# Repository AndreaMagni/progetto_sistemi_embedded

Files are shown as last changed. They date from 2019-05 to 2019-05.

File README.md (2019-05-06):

# Progetto Sistemi Embedded
Corso di Sistemi Embedded - Università degli Studi di Milano - Anno accademico 2017/2018

### Autori:
Magni Andrea - Mercanti Davide

### Descrizione progetto:
Il progetto che abbiamo deciso di realizzare prevede la costruzione di una "macchina intelligente".

La macchina andrà a svolgere diverse funzioni, principalmente di comunicazione o di valutazione e risoluzione di problematiche, tra le quali:

- riuscire a muoversi all'interno di una strada composta da due corsie, rimanendo all'interno di una corsia
- riuscire ad effettuare una manovra di cambio corsia
- valutare la presenza di un semaforo
  - nel caso in cui venga rilevato un semaforo valuti la sua condizione e regoli la velocità di conseguenza
- valutare la presenza di possibili ostacoli durante il percorso
  - nel caso in cui venga rilevato un ostacolo valuti il tipo di ostacolo (mobile o fisso) e decida se continuare il 
  percorso o effettuare una manovra di cambio corsia
- comunicare con un telefono per permettere lo scambio di informazioni tra la macchina e l'utente in diretta

### Componenti necessari:
- x1 | Arduino MEGA | https://www.amazon.it/gp/product/B06XRJNB27/ (necessario per la macchina, la quale richiede molti GPIO)
- x1 | Board generica per gestire il semaforo, il quale non necessità di molti GPIO
- x1 | 4 Motori - 4 Ruote - Scocca | https://www.amazon.it/gp/product/B073169GBF/ (si possono utilizzare solo due ruote/motori con una terza ruota girevole https://www.amazon.it/dp/B072ZWRM2B/)
- x2 | Modulo gestione motori - L298N | https://www.amazon.it/gp/product/B013QTC18K/ (si può utilizzare un solo modulo gestendo i motori a coppie)
- x2 | Modulo radio - NRF24L01 | https://www.amazon.it/gp/product/B016BAPC0K/ (si possono utilizzare eventualmente dei moduli Wi-Fi o Bluetooth)
- x1 | Modulo bluetooth - HC-05 | https://www.amazon.it/dp/B01G9KSAF6/
- x4 | Sensore ad infrarossi - TE174 o FC-35 | https://www.amazon.it/gp/product/B00XXEJD58/ 
- x3 | Sensore ad ultrasuoni - HC-SR04 | https://www.amazon.it/gp/product/B00R2U8HK6/
- x1 | Resistenza da 8.2 ohm (in alternativa 10)
- x3 | Resistenza da 220 ohm
- x1 | Resistenza da 1 Kohm
- x1 | Resistenza da 2.2 Kohm
- x1 | Resistenza da 10 Kohm
- Componenti vari come breadboard e cavetteria

### Sviluppo del progetto:
- Realizzazione di una macchina, la quale deve:
  - potersi muovere attraverso il controllo, in modo indipendente, della velocità e verso dei _**quattro motori DC**_. Questa funzionalità è permessa dalla presenza di due _**moduli gestione motori**_. Nello specifico per questo progetto viene utilizzato il _**modulo gestione motori L298N**_, il quale permette la gestione del verso e della potenza di due motori in modo indipendente.
  - valutare la corsia da seguire all'interno del tratto stradale. Per questa funzionalità abbiamo deciso di creare un inseguitore di linea, tramite dei _**sensori ad infrarossi**. 
  - valutare la presenza di ostacoli nel suo percorso tramite dei _**sensori ad ultrasuoni**_
  - valutare lo stato dei semafori tramite un _**modulo radio**_
- Realizzazione di una strada:
  - le opzioni per questo punto erano due, da un lato la semplice creazione di delle strisce nere da posizionare sul pavimento per permettere ai sensori ad infrarossi di valutare la strada da seguire oppure realizzare una strada vera e propria. Abbiamo deciso di realizzare una strada tramite del polistirolo cartonato, disegnando le linee tramite degli indelibili neri. La strada è composta da un totale di quattro linee, ogni corsia da due. La linea meno spessa serve alla macchina per stabilire da quale lato della strada si trova in modo da effettuare la giusta manovra nel caso in cui debba effettuare un cambio corsia. 
- Realizzazione di un semaforo, il quale deve:
  - effettuare un cambiamento di stato tra "verde giallo rosso".
  - comunicare con la macchina lo stato del semaforo
  
### Schema collegamenti macchina:
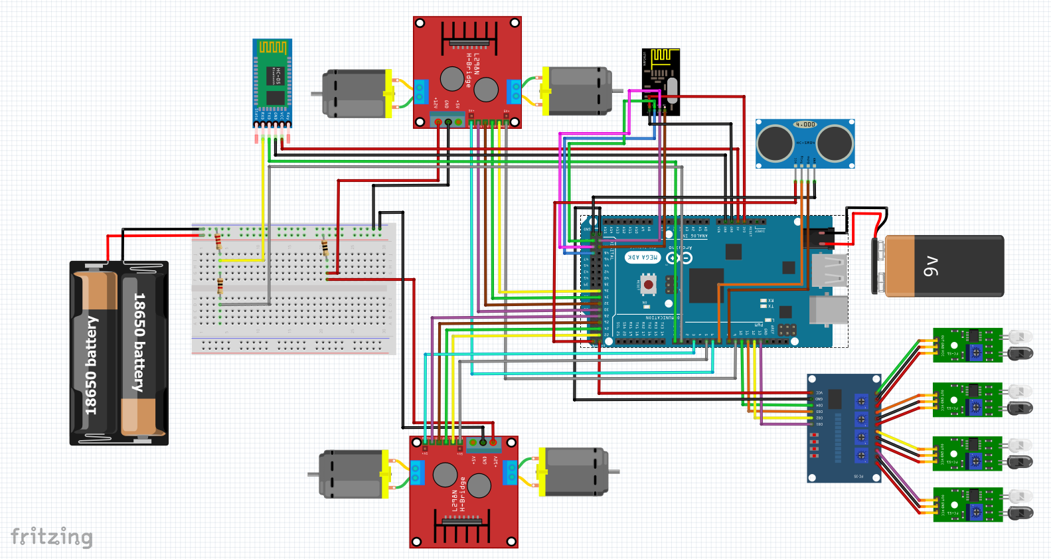
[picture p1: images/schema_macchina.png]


### Schema collegamenti semaforo:
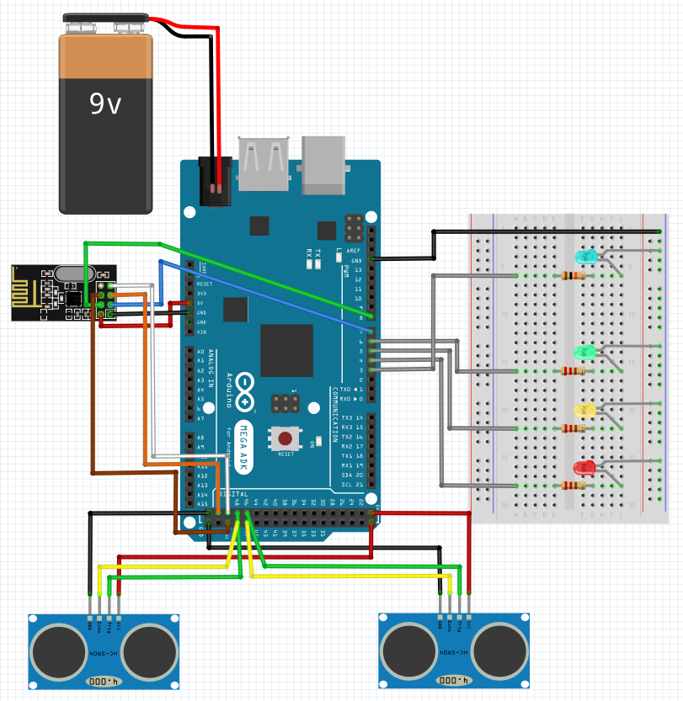
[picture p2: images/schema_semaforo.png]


### Foto:
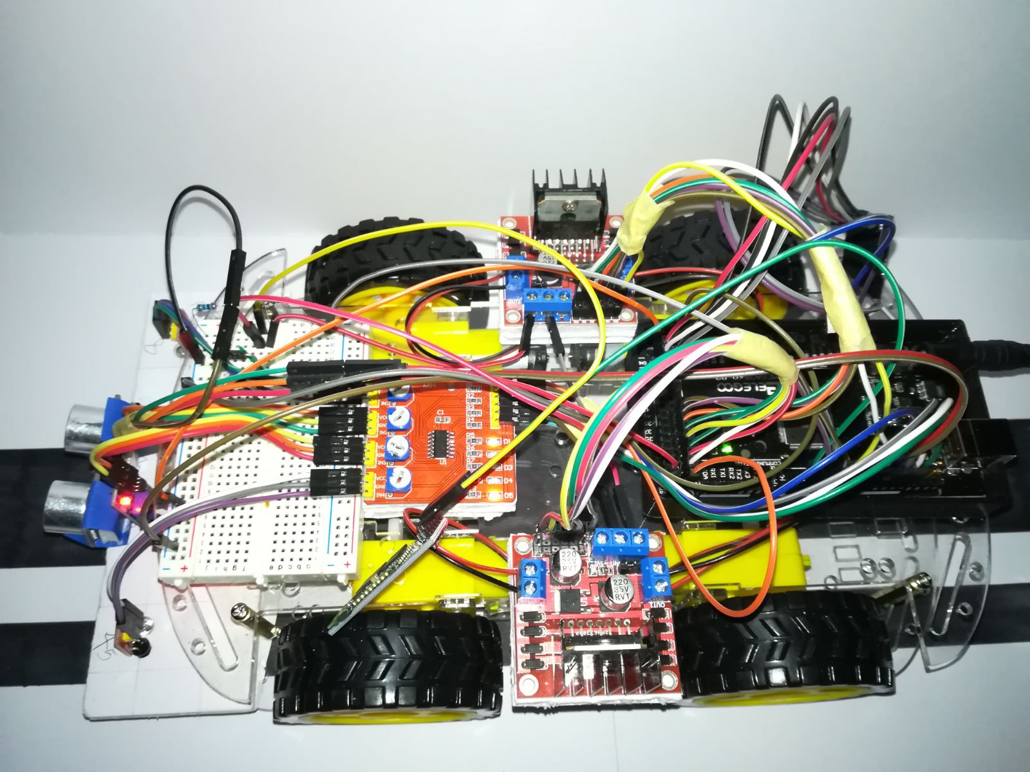
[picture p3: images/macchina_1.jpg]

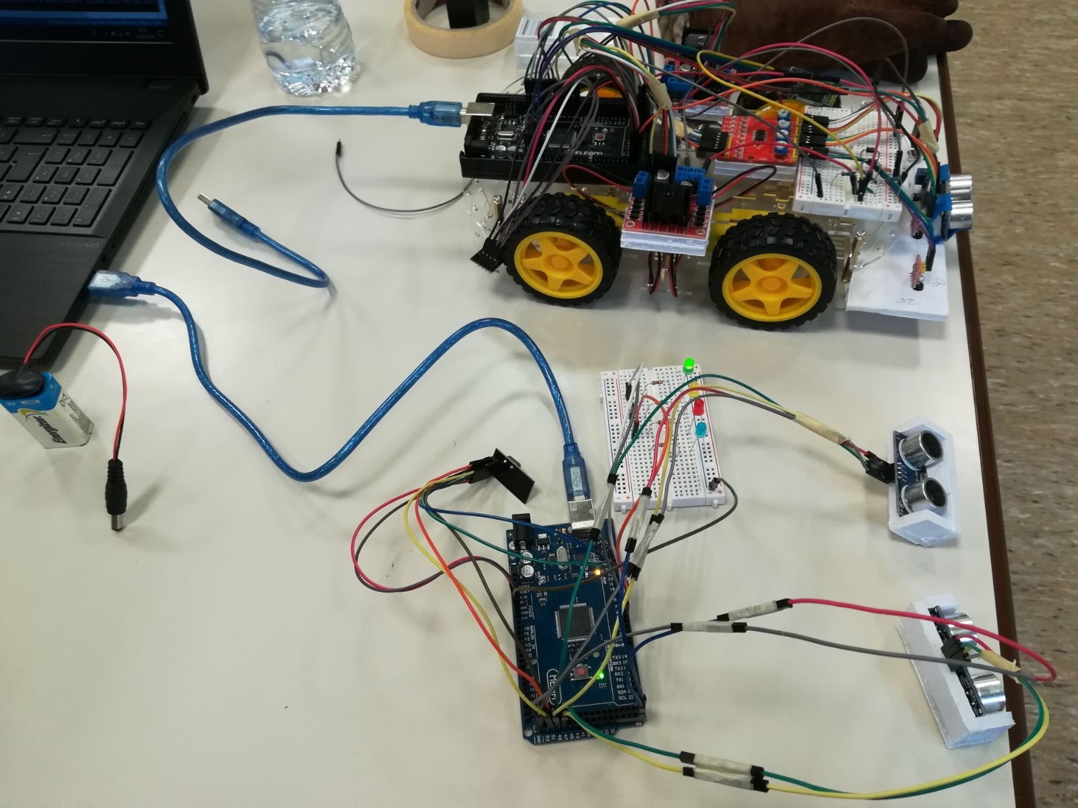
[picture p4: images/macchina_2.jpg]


### Video: 

Test sistema di gestione delle curve tramite servo:  
https://www.dropbox.com/s/mpuvc6oca1bey50/1_vecchio_sistema_curva.mp4?dl=0

Test sistema di gestione delle curve tramite velocità differenti sulle ruote:  
https://www.dropbox.com/s/kdcqv2tspdruida/2_nuovo_sistema_curva.mp4?dl=0

Test inseguitore di linea tramite infrarossi:  
https://www.dropbox.com/s/6vckf1oelf2ck3c/3_infrarossi_curva.mp4?dl=0

Test gestione velocità tramite ultrasuoni:  
https://www.dropbox.com/s/164yps8jlzu4az5/4_sonar_stop.mp4?dl=0

Prototipo finale con tracciato, gestione ostacolo fisso:  
https://www.dropbox.com/s/opallh4xtinxfd5/5_ostacolo_singolo.mp4?dl=0

Prototipo finale con tracciato, gestione doppio ostacolo fisso:  
https://www.dropbox.com/s/qxkiae7qwjshndc/6_doppio_ostacolo.mp4?dl=0

### Librerie aggiuntive:
- RF24.h (modulo radio): https://github.com/nRF24/RF24
- NewPing.h (sensore ultrasuoni): https://playground.arduino.cc/Code/NewPing
- Motor.h (gestione motori): https://github.com/AndreaMagni/SistemiEmbedded/tree/master/Car

### Possibili upgrade:
- Realizzazione di un sistema di semafori, ad esempio un incrocio, il quale valuti la presenza di cose di macchine nelle varie strade e decida come impostare i semafori in modo intelligente.
- Realizzazione di un sistema GPS per tenere traccia degli spostamenti della macchina, probabilmente sulla piccola scala dei movimenti della macchina potrebbe essere difficile o inutile da sviluppare ma potrebbe portare ad idee alternative collegate.
- Realizzazione di un collegamento tra la macchina e Processing scrivendo del codice per ricreare il tracciato percorso dalla macchina durante ogni sessione di utilizzo.
- Realizzazione di un sistema di sterzo per permettere alla macchina di curvare.
- Realizzazione di un sonar mobile, creato unendo un sensore ad ultrasuoni ad un servomotore. In questo modo sarebbe possibile analizzare le distanze degli oggetti non solo se frontali rispetto al modulo ad ultrasuoni ma anche attorno ad esso.
- Realizzazione di un passaggio a livello tramite un servomotore

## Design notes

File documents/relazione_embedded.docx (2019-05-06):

DESCRIZIONE FUNZIONALITA’

Il progetto che abbiamo deciso di realizzare prevede la costruzione di una "macchina intelligente".

La macchina andrà a svolgere diverse funzioni, principalmente di comunicazione o di valutazione e risoluzione di problematiche, tra le quali:

- riuscire a muoversi all'interno di una strada composta da due corsie, rimanendo all'interno di una corsia
- riuscire ad effettuare una manovra di cambio corsia
- valutare la presenza di un semaforo
  - nel caso in cui venga rilevato un semaforo valuti la sua condizione e regoli la velocità di conseguenza
- valutare la presenza di possibili ostacoli durante il percorso
  - nel caso in cui venga rilevato un ostacolo valuti il tipo di ostacolo (mobile o fisso) e decida se continuare il percorso o effettuare una manovra di cambio corsia
- comunicare con un telefono per permettere lo scambio di informazioni tra la macchina e l'utente in diretta

ELENCO COMPONENTI

Quantità | Componente | Link Amazon
1 | Board Arduino Mega | https://www.amazon.it/dp/B06XRJNB27/
1 | Board generica (non sono necessari molti GPIO) | https://www.amazon.it/dp/B01MRJR8UF/
1 | Kit telaio ruote motori | https://www.amazon.it/dp/B073169GBF/
| | https://www.amazon.it/dp/B072ZWRM2B/
2 | Modulo gestione motori - L298N | https://www.amazon.it/dp/B013QTC18K/
2 | Modulo radio - nRF24L01 | https://www.amazon.it/dp/B016BAPC0K/
1 | Modulo bluetooth - HC-05 | https://www.amazon.it/dp/B01G9KSAF6/
4 | Sensore ad infrarossi - TE174 o FC-35 | https://www.amazon.it/dp/B00XXEJD58/
3 | Sensore ad ultrasuoni - HC-SR04 | https://www.amazon.it/dp/B00R2U8HK6/
1 | Resistenza x | https://www.amazon.it/ dp/B00J02WSFE/
1 | Resistenza x
1 | Resistenza x AL POSTO DEI DIODI
2 | Breadboard | https://www.amazon.it/ dp/B06XRDRT2R/
1 | Cavetteria | https://www.amazon.it/ dp/B01N40EK6M/ (https://www.amazon.it/%20dp/B01N40EK6M/)

DESCRIZIONE COMPONENTI UTILIZZATI

Per la creazione di questo progetto sono stati utilizzati diversi componenti, aggiungendo sempre più funzionalità potendo così testare il funzionamento di diversi sensori e moduli con relative interazioni all’interno di un singolo progetto. Andremo ora ad analizzare i vari componenti:

Telaio / Motori / Ruote

Per realizzare questo progetto è fondamentale una scocca che permetta alla macchina di sostenere i vari componenti e successivamente, una volta realizzato il codice e inseriti i vari sensori e moduli, muoversi all’interno del tracciato.

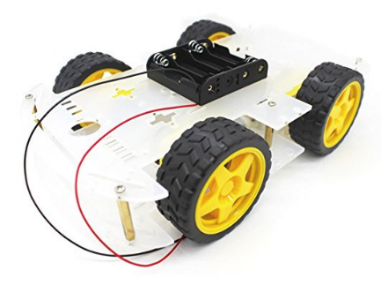
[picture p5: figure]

Sicuramente è un componente il cui acquisto non è necessario (sarebbe stato possibile crearlo attraverso del cartone) avendo però la necessità di comprare delle ruote e relativi motori a corrente continua la differenza di costo tra il comprare un kit telaio/motori/ruote oppure delle ruote e motori singolarmente era irrosoria se non addirittura più conveniente. Abbiamo quindi optato per questo telaio realizzato in plexiglass. I motori messi a disposizione nel kit sono dei comunissimi motori a corrente continua ai quali è possibile fornire una tensione massima di 6 Volt. Le ruote sono un mix di plastica e gomma.

Per quanto questo kit abbia comportato grandi comodità, bisogna anche dire che i motori non sono particolarmente precisi. Questo comporta la presenza di piccole imprecisioni durante la guida automatica della macchina che possono essere notate durante il suo percorso. Non dovendo però andare a realizzare un progetto che punta sulla precisione, la comodità portata dal kit unita al costo irrosorio ne fanno un acquisto decisamente sensato per il progetto.

Modulo L298N

Questo modulo è sicuramente un acquisto necessario quando si vuole realizzare un progetto di questo genere.

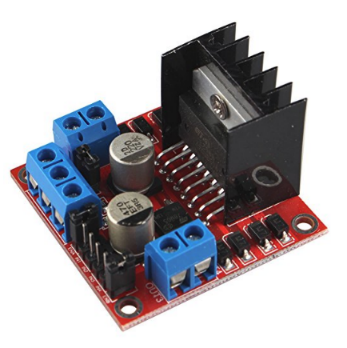
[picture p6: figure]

Il modulo L298N è utilizzato per comandare fino ad un massimo di due motori a corrente continua, può funzionare con tensioni che variano dai 5 ai 35 Volt e fornire sino a 2 Ampere di corrente per ogni uscita. Particolarmente utile la presenza di un’uscita stabile a 5 Volt, la quale può essere utilizzata per alimentare Arduino, dei componenti oppure per far passare 5 Volt sulla breadboard.

Per il progetto sono stati utilizzati due di questi componenti, potendo così gestire singolarmente ogni motore. Questa soluzione non è necessaria in quanto si potrebbe utilizzare un solo modulo collegando in parallelo a coppie i motori.

Modulo nRF24L01

Questo modulo viene utilizzato per creare un canale radio attraverso il quale comunicare. Esso non è necessario nel momento in cui si vuole costruire un semplice line follower, invece può risultare molto utile nel momento in cui si voglia comunicare con altri componenti (ad esempio un radiocomando per controllare la macchina).

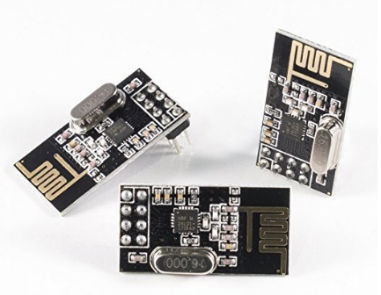
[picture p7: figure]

All’interno del progetto è stato inserito per permettere la comunicazione con un secondo Arduino, all’interno del quale è caricato un programma che simula un semaforo.

Il semaforo e la macchina potranno quindi comunicare tra loro, nello specifico sarà il semaforo che potrà inviare alla macchina il suo stato, la macchina andrà ad analizzare lo stato corrente e valuterà in base allo stato come comportarsi.

Modulo HC-05

Questo modulo non è sicuramente un acquisto necessario per il progetto, in quanto un eventuale connessione tra Arduino e un secondo Arduino è già permessa dal modulo radio.

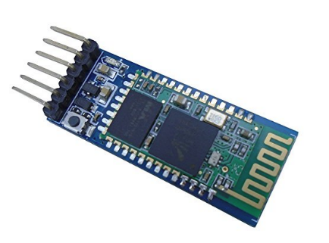
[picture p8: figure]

La scelta di aggiungere un modulo la cui funzione è quella di creare una connessione Bluetooth è stata fatta per due motivi, il principale è quello di poter comunicare con un telefono tramite una delle tante applicazioni presenti sugli store e poter così effettuare un debug in live, molto utile per determinare problemi nel comportamento della macchina in fase di progettazione. In precedenza al posto del Bluetooth era presente un display LCD sul quale venivano mostrate le informazioni. Il secondo motivo è la possibilità di avere una connessione senza fili con un PC con cui scambiare dati nel caso in cui si vogliano sviluppare in futuro delle applicazioni con Processing per visualizzare il movimento della macchina.

Sensore HC-SR04

Questo sensore permette di valutare la distanza tra esso ed un oggetto tramite l’utilizzo di ultrasuoni.

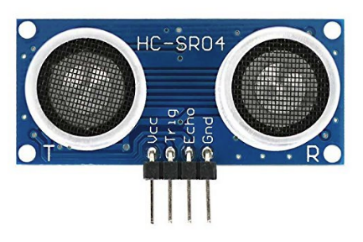
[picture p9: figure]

Trova un doppio utilizzo all’interno del progetto poiché risulta utile sia per la macchina che per il semaforo. Per la macchina la sua funzione è quella di permettere alla macchina di valutare la presenza di eventuali ostacoli di fronte al suo percorso, invece per quanto riguarda il semaforo il suo utilizzo è quello di creare una zona di apertura e una di chiusura di invio del segnale radio, impedendo cosi eventuali problemi dati da un segnale continuo.

Sensore FC-35 / FC-51

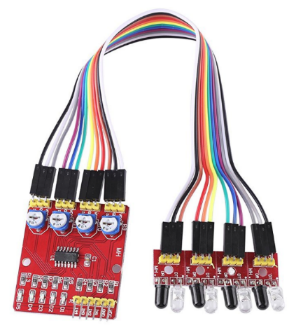
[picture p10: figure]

Questo modulo viene utilizzato per creare Questo modulo viene utilizzato per creare

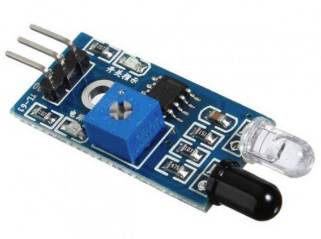
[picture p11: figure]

Questo modulo viene utilizzato per creare

Questo modulo viene utilizzato per creare

Questo modulo viene utilizzato per creare

Componentistica varia

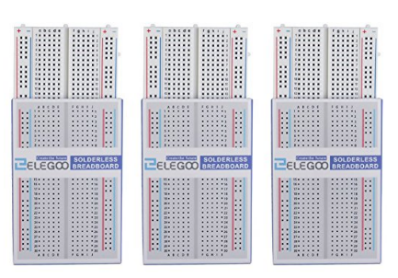
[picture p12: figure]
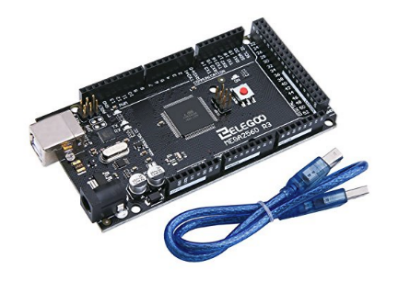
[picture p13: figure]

Per concludere, gli altri componenti utilizzati per il progetti sono una piattaforma Arduino Mega e relativa breadboard per comandare i vari moduli e sensori della macchina, un secondo Arduino Mega con breadboard per creare il semaforo.

Inoltre è stata usata molta cavetteria, dei diodi generici la cui funzione è quella di abbassare la tensione erogata dalla batteria che comanda la macchina, una resistenza da 3Kohm e una da 1Kohm, dei led per mostrare lo stato del semaforo, due pile 18650 da 3.7 Volt, due pile da 9 Volt per alimentare i due Arduino.

CODICE REALIZZATO

Per la realizzazione di questo progetto sono stati creati quattro file:

- macchina.ino per la gestione della macchina
- semaforo.ino per la gestione del semaforo
- motor.h e motor.cpp una libreria creata appositamente per il progetto

/*

* Nome file: macchina.ino

*

* Questo programma permette alla macchina, attraverso diverse funzioni, sensori e moduli di poter valutare

* ed interagire con l’esterno. Nello specifico la macchina dovrà riuscire a muoversi all’interno di una strada

* appositamente creata e comunicare attraverso segnali Bluetooth e Radio con altri oggetti.

*

* Informazioni dettagliate al seguente link: https://github.com/AndreaMagni/SistemiEmbedded/
*

* Copyright © 2018, Magni Andrea & Mercanti Davide

*

* This program is free software: you can redistribute it and/or modify it under the terms of the GNU General

* Public License as published by the Free Software Foundation, either version 3 of the License, or (at your option)

* any later version.

*

* This program is distributed in the hope that it will be useful, but WITHOUT ANY WARRANTY; without even the

* implied warranty of MERCHANTABILITY or FITNESS FOR A PARTICULAR PURPOSE. See the GNU General Public

* License for more details.

*

* You should have received a copy of the GNU General Public License with this program.

* If not, see <http://www.gnu.org/licenses/>.

*/

/*

* Inclusione librerie necessarie per il funzionamento del programma

* NewPing.h utilizzata per la gestione dei sensori ad ultrasuoni

* SPI.h utilizzata per la comunicazione con dispositivi SPI (serial peripheral interface)

* nRF24L01.h utilizzata per la gestione dei moduli radio

* RF24.h utilizzata per la gestione dei moduli radio

* Motor.h creata per semplificare l’utilizzo dei motori

*/

#include <NewPing.h>

#include <SPI.h>

#include <nRF24L01.h> UNA DI QUESTE DUE

#include <RF24.h> UNA DI QUESTE DUE

#include <Motor.h>

/*

* Definizione sensori ad infrarossi (nessun ostacolo rilevato [1] - ostacolo rilevato [0])

* DETECT_ED - Sensore esterno destro

* DETECT_CD - Sensore centrale destro

* DETECT_CS - Sensore centrale sinistro

* DETECT_ES - Sensore esterno sinistro

*/

#define DETECT_ED 10

#define DETECT_ED 11

#define DETECT_CS 12

#define DETECT_ES 13

/*

* Definizione variabile per effettuare il debug via bluetooth (abilitato [1] - disabilitato [0])

* Utilizzare solo se strettamente necessario vista la presenza di delay nel debug

* i quali possono portare ad un rallentamento delle funzioni della macchina

*/

#define DEBUG 0

/*

* Dichiarazione e assegnazione di diverse variabili. Nello specifico:

* turn_left: utilizzata per

* turn_right: utilizzata per

* pipe: utilizzata per definire l’indirizzo di comunicazione radio

* channel: utilizzata per definire il channel all’interno dell’indirizzo di comunicazione radio

*/

bool turn_left = false;

bool turn_right = false;

const uint64_t pipe = 0xABCDEF;

const uint8_t channel = 0x1;

/*

* Creazione oggetti

* sonar(trigger_pin, echo_pin, max_cm_distance)

* mt(speed_[m1, m2, m3, m4], dir_a_[m1, m2, m3, m4], dir_b_[m1, m2, m3, m4])

* radio(ce, csn)

*/

NewPing sonar(7, 8, 200);

Motor mt(5, 3, 9, 6, 22, 26, 30, 34, 24, 28, 32, 36);

RF24 radio(49, 53);

/*

* Funzione secureDigitalRead(int pin)

* La funzione permette

*/

bool secureDigitalRead(int pin) {

bool register tmp1, tmp2, tmp3;

tmp1 = digitalRead(pin);

delay(2);

tmp2 = digitalRead(pin);

delay(2);

tmp3 = digitalRead(pin);

return (tmp1&&tmp2) || (tmp2&&tmp3) || (tmp1&&tmp3);

}

/*

* Funzione obstacleDetection()

* La funzione permette

*/

bool obstacleDetection() {

int pingTime = sonar.ping_median(5);

int distance = sonar.convert_cm(pingTime);

if (distance <= 15) return true;

else return false;

}

/*

* Funzione segnaleSemaforo()

* La funzione permette

*/

char* segnaleSemaforo() { // DA MODIFICARE ASSOLUTAMENTE

if (radio.available()) {

char text[5] = "";

radio.read(&text, sizeof(text));

if (strcmp(text, "001") == 0) {

return ((char *)"rosso");

} else if (strcmp(text, "010") == 0) {

return ((char *)"giallo");

} else if (strcmp(text, "100") == 0) {

return ((char *)"verde");

} else {

return ((char *)"errore");

}

}

}

void setup() {

if (DEBUG) {mySerial.begin(9600);}

pinMode(DETECT_ED, INPUT); // Definizione modalità input per il pin relativo al sensore infrarossi esterno destro

pinMode(DETECT_CD, INPUT); // Definizione modalità input per il pin relativo al sensore infrarossi centrale destro

pinMode(DETECT_CS, INPUT); // Definizione modalità input per il pin relativo al sensore infrarossi centrale sinistro

pinMode(DETECT_ES, INPUT); // Definizione modalità input per il pin relativo al sensore infrarossi esterno sinistro

radio.begin();

radio.setChannel(channel);

radio.openReadingPipe(0, pipe);

radio.setPALevel(RF24_PA_MIN);

radio.startListening(); //INSERIRE COME CONDIZIONE

}

void loop() {

if (DEBUG) {delay(1000); mySerial.write("Rilevazione infrarossi (1 = Libero / 0 = Ostacolo)"); mySerial.write("Sensore esterno destro: "); mySerial.write(digitalRead(DETECT_ED)); Serial.print(" - "); Serial.print("Sensore centrale destro: ");

mySerial.write(digitalRead(DETECT_CD)); mySerial.write(" - "); mySerial.write("Sensore centrale sinistro: "); Serial.print(digitalRead(DETECT_CS)); Serial.print(" - "); Serial.print("Sensore esterno sinistro: ");

Serial.println(digitalRead(DETECT_ES)); Serial.println("---------------"); Serial.println("Rilevazione ultrasuono"); int pingTime = sonar.ping_median(5); Serial.print("Ping time: "); Serial.print(pingTime); Serial.print(" sec");

Serial.print(" - "); int distance = sonar.convert_cm(pingTime); Serial.print("Distance: "); Serial.print(distance); Serial.println(" cm"); Serial.println("---------------");}

char* test = segnaleSemaforo();

if (strcmp(test, "rosso") == 0) {

mt.car_stop();

if (DEBUG) {Serial.println("Rilevazione manovra in corso"); Serial.println("STOP 0"); Serial.println("---------------"); Serial.println("Rilevazione stato semaforo: "); Serial.println("rosso"); Serial.println("");}

} else {

if (obstacleDetection() && !turn_left && secureDigitalRead(DETECT_ED) && secureDigitalRead(DETECT_CD) && secureDigitalRead(DETECT_CS)) { // Verifica se la macchina puo' curvare:

mt.car_stop();

delay(5000);

if (obstacleDetection()) {

turn_left = true;

if (DEBUG) {mySerial.write("Rilevazione manovra in corso"); mySerial.write("Cambio corsia - Gira (da destra a sinistra)");}

mt.car_backward(85);

delay(500);

mt.car_left(170, 170, 170, 170);

delay(800);

if (DEBUG) {mySerial.write("Rilevazione manovra in corso"); mySerial.write("Cambio corsia - Avanti (da destra a sinistra)")}

//mt.car_forward(70);

//delay(100);

}

} else if (obstacleDetection() && !turn_right && secureDigitalRead(DETECT_ES) && secureDigitalRead(DETECT_CD) && secureDigitalRead(DETECT_CS)) { // Verifica se la macchina puo' curvare:

mt.car_stop();

delay(5000);

if (obstacleDetection()) {

turn_right = true;

if (DEBUG) {lcd.clear(); lcd.print("CC-CURVA-SaD "); lcd.print(SPEED_4); Serial.println("Rilevazione manovra in corso"); Serial.print("CAMBIO CORSIA - CURVA (da sinistra a destra) "); Serial.println(SPEED_4); Serial.println("");}

mt.car_backward(85);

delay(500);

mt.car_right(170, 170, 170, 170);

delay(800);

if (DEBUG) {lcd.clear(); lcd.print("CC-AVANTI-P-SaD "); lcd.print(SPEED_3); Serial.println("Rilevazione mnovra in corso"); Serial.print("CAMBIO CORSIA - AVANTI PRIMARIO (da sinistra a destra) "); Serial.println(SPEED_3); Serial.println("");}

//mt.car_forward(70);

//delay(100);

}

}

if (turn_left) {

if (secureDigitalRead(DETECT_CD)) {

turn_left = false;

while (secureDigitalRead(DETECT_CD) && !(secureDigitalRead(DETECT_CS))) {

mt.car_right(230, 230, 230, 230);

}

} else {

mt.car_forward(70);

if (DEBUG) {mySerial.write("CC-AVANTI-S-DaS "); mySerial.write("CAMBIO CORSIA - AVANTI SECONDARIO (da destra a sinistra) ");}

}

} else if (turn_right) {

if (secureDigitalRead(DETECT_CS)) {

turn_right = false;

while (secureDigitalRead(DETECT_CS) && !(secureDigitalRead(DETECT_CD))) {

mt.car_left(230, 230, 230, 230);

}

} else {

mt.car_forward(70);

if (DEBUG) {mySerial.write("CC-AVANTI-S-SaD "); mySerial.write("CAMBIO CORSIA - AVANTI SECONDARIO (da sinistra a destra)");}

}

} else {

if (digitalRead(DETECT_CD) && digitalRead(DETECT_CS)) {

if (DEBUG) {mySerial.write("Avanti");}

mt.car_forward(75);

} else if (!(digitalRead(DETECT_CD)) && digitalRead(DETECT_CS)) {

if (DEBUG) {mySerial.write("Sinistra");}

mt.car_left(130, 135, 130, 135);

} else if (digitalRead(DETECT_CD) && !(digitalRead(DETECT_CS))) {

if (DEBUG) {mySerial.write("Destra");}

mt.car_right(135, 130, 135, 130);

} else if (!(digitalRead(DETECT_CD)) && !(digitalRead(DETECT_CS))) {

if (DEBUG) {mySerial.write("Stop");}

mt.car_stop();

}

}

}

if (DEBUG) {mySerial.write("///////////////////////");}

}

/*

* Nome file: Motor.h

*

* Questo libreria è stata appositamente creata per poter gestier al meglio i motori vista la presenza di

* un due ponti H all’interno del nostro progetto. La classe Motor presenta diversi costruttori, uno per definire

* l’oggetto Motor e delle funzioni (avanti, indietro, destra, sinistra) con singolo o multiplo attributo.

*

* Informazioni dettagliate al seguente link: https://github.com/AndreaMagni/SistemiEmbedded/
*

* Copyright © 2018, Magni Andrea & Mercanti Davide

*

* This program is free software: you can redistribute it and/or modify it under the terms of the GNU General

* Public License as published by the Free Software Foundation, either version 3 of the License, or (at your option)

* any later version.

*

* This program is distributed in the hope that it will be useful, but WITHOUT ANY WARRANTY; without even the

* implied warranty of MERCHANTABILITY or FITNESS FOR A PARTICULAR PURPOSE. See the GNU General Public

* License for more details.

*

* You should have received a copy of the GNU General Public License with this program.

* If not, see <http://www.gnu.org/licenses/>.

*/

#ifndef Motor_h

#define Motor_h

#include "Arduino.h"

class Motor {

public:

Motor(int PIN_SPEED_M1, int PIN_SPEED_M2, int PIN_SPEED_M3, int PIN_SPEED_M4,

int PIN_DIR_A_M1, int PIN_DIR_A_M2, int PIN_DIR_A_M3, int PIN_DIR_A_M4,

int PIN_DIR_B_M1, int PIN_DIR_B_M2, int PIN_DIR_B_M3, int PIN_DIR_B_M4);

void car_forward(int SPEED);

void car_backward(int SPEED);

void car_left(int SPEED);

void car_right(int SPEED);

void car_forward(int SPEED_1, int SPEED_2, int SPEED_3, int SPEED_4);

void car_backward(int SPEED_1, int SPEED_2, int SPEED_3, int SPEED_4);

void car_left(int SPEED_1, int SPEED_2, int SPEED_3, int SPEED_4);

void car_right(int SPEED_1, int SPEED_2, int SPEED_3, int SPEED_4);

void car_stop();

private:

int _PIN_SPEED_M1;

int _PIN_SPEED_M2;

int _PIN_SPEED_M3;

int _PIN_SPEED_M4;

int _PIN_DIR_A_M1;

int _PIN_DIR_A_M2;

int _PIN_DIR_A_M3;

int _PIN_DIR_A_M4;

int _PIN_DIR_B_M1;

int _PIN_DIR_B_M2;

int _PIN_DIR_B_M3;

int _PIN_DIR_B_M4;

};

#endif

/*

* Nome file: Motor.ccp

*

* Questo libreria è stata appositamente creata per poter gestier al meglio i motori vista la presenza di

* un due ponti H all’interno del nostro progetto. La classe Motor presenta diversi costruttori, uno per definire

* l’oggetto Motor e delle funzioni (avanti, indietro, destra, sinistra) con singolo o multiplo attributo.

*

* Informazioni dettagliate al seguente link: https://github.com/AndreaMagni/SistemiEmbedded/
*

* Copyright © 2018, Magni Andrea & Mercanti Davide

*

* This program is free software: you can redistribute it and/or modify it under the terms of the GNU General

* Public License as published by the Free Software Foundation, either version 3 of the License, or (at your option)

* any later version.

*

* This program is distributed in the hope that it will be useful, but WITHOUT ANY WARRANTY; without even the

* implied warranty of MERCHANTABILITY or FITNESS FOR A PARTICULAR PURPOSE. See the GNU General Public

* License for more details.

*

* You should have received a copy of the GNU General Public License with this program.

* If not, see <http://www.gnu.org/licenses/>.

*/

#include "Arduino.h"

#include "Motor.h"

Motor::Motor(int PIN_SPEED_M1, int PIN_SPEED_M2, int PIN_SPEED_M3, int PIN_SPEED_M4, int PIN_DIR_A_M1,

int PIN_DIR_A_M2, int PIN_DIR_A_M3, int PIN_DIR_A_M4, int PIN_DIR_B_M1, int PIN_DIR_B_M2,

int PIN_DIR_B_M3, int PIN_DIR_B_M4) {

pinMode(PIN_SPEED_M1, OUTPUT);

pinMode(PIN_DIR_A_M1, OUTPUT);

pinMode(PIN_DIR_B_M1, OUTPUT);

pinMode(PIN_SPEED_M2, OUTPUT);

pinMode(PIN_DIR_A_M2, OUTPUT);

pinMode(PIN_DIR_B_M2, OUTPUT);

pinMode(PIN_SPEED_M3, OUTPUT);

pinMode(PIN_DIR_A_M3, OUTPUT);

pinMode(PIN_DIR_B_M3, OUTPUT);

pinMode(PIN_SPEED_M4, OUTPUT);

pinMode(PIN_DIR_A_M4, OUTPUT);

pinMode(PIN_DIR_B_M4, OUTPUT);

_PIN_SPEED_M1 = PIN_SPEED_M1;

_PIN_DIR_A_M1 = PIN_DIR_A_M1;

_PIN_DIR_B_M1 = PIN_DIR_B_M1;

_PIN_SPEED_M2 = PIN_SPEED_M2;

_PIN_DIR_A_M2 = PIN_DIR_A_M2;

_PIN_DIR_B_M2 = PIN_DIR_B_M2;

_PIN_SPEED_M3 = PIN_SPEED_M3;

_PIN_DIR_A_M3 = PIN_DIR_A_M3;

_PIN_DIR_B_M3 = PIN_DIR_B_M3;

_PIN_SPEED_M4 = PIN_SPEED_M4;

_PIN_DIR_A_M4 = PIN_DIR_A_M4;

_PIN_DIR_B_M4 = PIN_DIR_B_M4;

}

void Motor::car_forward(int SPEED) {

analogWrite(_PIN_SPEED_M1, SPEED);

analogWrite(_PIN_SPEED_M2, SPEED);

analogWrite(_PIN_SPEED_M3, SPEED);

analogWrite(_PIN_SPEED_M4, SPEED);

digitalWrite(_PIN_DIR_A_M1, LOW);

digitalWrite(_PIN_DIR_B_M1, HIGH);

digitalWrite(_PIN_DIR_A_M2, LOW);

digitalWrite(_PIN_DIR_B_M2, HIGH);

digitalWrite(_PIN_DIR_A_M3, LOW);

digitalWrite(_PIN_DIR_B_M3, HIGH);

digitalWrite(_PIN_DIR_A_M4, LOW);

digitalWrite(_PIN_DIR_B_M4, HIGH);

}

void Motor::car_forward(int SPEED_1, int SPEED_2, int SPEED_3, int SPEED_4) {

analogWrite(_PIN_SPEED_M1, SPEED_1);

analogWrite(_PIN_SPEED_M2, SPEED_2);

analogWrite(_PIN_SPEED_M3, SPEED_3);

analogWrite(_PIN_SPEED_M4, SPEED_4);

digitalWrite(_PIN_DIR_A_M1, LOW);

digitalWrite(_PIN_DIR_B_M1, HIGH);

digitalWrite(_PIN_DIR_A_M2, LOW);

digitalWrite(_PIN_DIR_B_M2, HIGH);

digitalWrite(_PIN_DIR_A_M3, LOW);

digitalWrite(_PIN_DIR_B_M3, HIGH);

digitalWrite(_PIN_DIR_A_M4, LOW);

digitalWrite(_PIN_DIR_B_M4, HIGH);

}

void Motor::car_backward(int SPEED) {

analogWrite(_PIN_SPEED_M1, SPEED);

analogWrite(_PIN_SPEED_M2, SPEED);

analogWrite(_PIN_SPEED_M3, SPEED);

analogWrite(_PIN_SPEED_M4, SPEED);

digitalWrite(_PIN_DIR_A_M1, HIGH);

digitalWrite(_PIN_DIR_B_M1, LOW);

digitalWrite(_PIN_DIR_A_M2, HIGH);

digitalWrite(_PIN_DIR_B_M2, LOW);

digitalWrite(_PIN_DIR_A_M3, HIGH);

digitalWrite(_PIN_DIR_B_M3, LOW);

digitalWrite(_PIN_DIR_A_M4, HIGH);

digitalWrite(_PIN_DIR_B_M4, LOW);

}

void Motor::car_backward(int SPEED_1, int SPEED_2, int SPEED_3, int SPEED_4) {

analogWrite(_PIN_SPEED_M1, SPEED_1);

analogWrite(_PIN_SPEED_M2, SPEED_2);

analogWrite(_PIN_SPEED_M3, SPEED_3);

analogWrite(_PIN_SPEED_M4, SPEED_4);

digitalWrite(_PIN_DIR_A_M1, HIGH);

digitalWrite(_PIN_DIR_B_M1, LOW);

digitalWrite(_PIN_DIR_A_M2, HIGH);

digitalWrite(_PIN_DIR_B_M2, LOW);

digitalWrite(_PIN_DIR_A_M3, HIGH);

digitalWrite(_PIN_DIR_B_M3, LOW);

digitalWrite(_PIN_DIR_A_M4, HIGH);

digitalWrite(_PIN_DIR_B_M4, LOW);

}

void Motor::car_left(int SPEED) {

analogWrite(_PIN_SPEED_M1, SPEED);

analogWrite(_PIN_SPEED_M2, SPEED);

analogWrite(_PIN_SPEED_M3, SPEED);

analogWrite(_PIN_SPEED_M4, SPEED);

digitalWrite(_PIN_DIR_A_M1, HIGH);

digitalWrite(_PIN_DIR_B_M1, LOW);

digitalWrite(_PIN_DIR_A_M2, LOW);

digitalWrite(_PIN_DIR_B_M2, HIGH);

digitalWrite(_PIN_DIR_A_M3, HIGH);

digitalWrite(_PIN_DIR_B_M3, LOW);

digitalWrite(_PIN_DIR_A_M4, LOW);

digitalWrite(_PIN_DIR_B_M4, HIGH);

}

void Motor::car_left(int SPEED_1, int SPEED_2, int SPEED_3, int SPEED_4) {

analogWrite(_PIN_SPEED_M1, SPEED_1);

analogWrite(_PIN_SPEED_M2, SPEED_2);

analogWrite(_PIN_SPEED_M3, SPEED_3);

analogWrite(_PIN_SPEED_M4, SPEED_4);

digitalWrite(_PIN_DIR_A_M1, HIGH);

digitalWrite(_PIN_DIR_B_M1, LOW);

digitalWrite(_PIN_DIR_A_M2, LOW);

digitalWrite(_PIN_DIR_B_M2, HIGH);

digitalWrite(_PIN_DIR_A_M3, HIGH);

digitalWrite(_PIN_DIR_B_M3, LOW);

digitalWrite(_PIN_DIR_A_M4, LOW);

digitalWrite(_PIN_DIR_B_M4, HIGH);

}

void Motor::car_right(int SPEED) {

analogWrite(_PIN_SPEED_M1, SPEED);

analogWrite(_PIN_SPEED_M2, SPEED);

analogWrite(_PIN_SPEED_M3, SPEED);

analogWrite(_PIN_SPEED_M4, SPEED);

digitalWrite(_PIN_DIR_A_M1, LOW);

digitalWrite(_PIN_DIR_B_M1, HIGH);

digitalWrite(_PIN_DIR_A_M2, HIGH);

digitalWrite(_PIN_DIR_B_M2, LOW);

digitalWrite(_PIN_DIR_A_M3, LOW);

digitalWrite(_PIN_DIR_B_M3, HIGH);

digitalWrite(_PIN_DIR_A_M4, HIGH);

digitalWrite(_PIN_DIR_B_M4, LOW);

}

void Motor::car_right(int SPEED_1, int SPEED_2, int SPEED_3, int SPEED_4) {

analogWrite(_PIN_SPEED_M1, SPEED_1);

analogWrite(_PIN_SPEED_M2, SPEED_2);

analogWrite(_PIN_SPEED_M3, SPEED_3);

analogWrite(_PIN_SPEED_M4, SPEED_4);

digitalWrite(_PIN_DIR_A_M1, LOW);

digitalWrite(_PIN_DIR_B_M1, HIGH);

digitalWrite(_PIN_DIR_A_M2, HIGH);

digitalWrite(_PIN_DIR_B_M2, LOW);

digitalWrite(_PIN_DIR_A_M3, LOW);

digitalWrite(_PIN_DIR_B_M3, HIGH);

digitalWrite(_PIN_DIR_A_M4, HIGH);

digitalWrite(_PIN_DIR_B_M4, LOW);

}

void Motor::car_stop() {

analogWrite(_PIN_SPEED_M1, 0);

analogWrite(_PIN_SPEED_M2, 0);

analogWrite(_PIN_SPEED_M3, 0);

analogWrite(_PIN_SPEED_M4, 0);

digitalWrite(_PIN_DIR_A_M1, LOW);

digitalWrite(_PIN_DIR_B_M1, LOW);

digitalWrite(_PIN_DIR_A_M2, LOW);

digitalWrite(_PIN_DIR_B_M2, LOW);

digitalWrite(_PIN_DIR_A_M3, LOW);

digitalWrite(_PIN_DIR_B_M3, LOW);

digitalWrite(_PIN_DIR_A_M4, LOW);

digitalWrite(_PIN_DIR_B_M4, LOW);

}

Anno accademico 2017/2018Sistemi EmbeddedMagni Andrea & Mercanti Davide

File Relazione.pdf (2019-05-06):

| Anno accademico 2017/2018

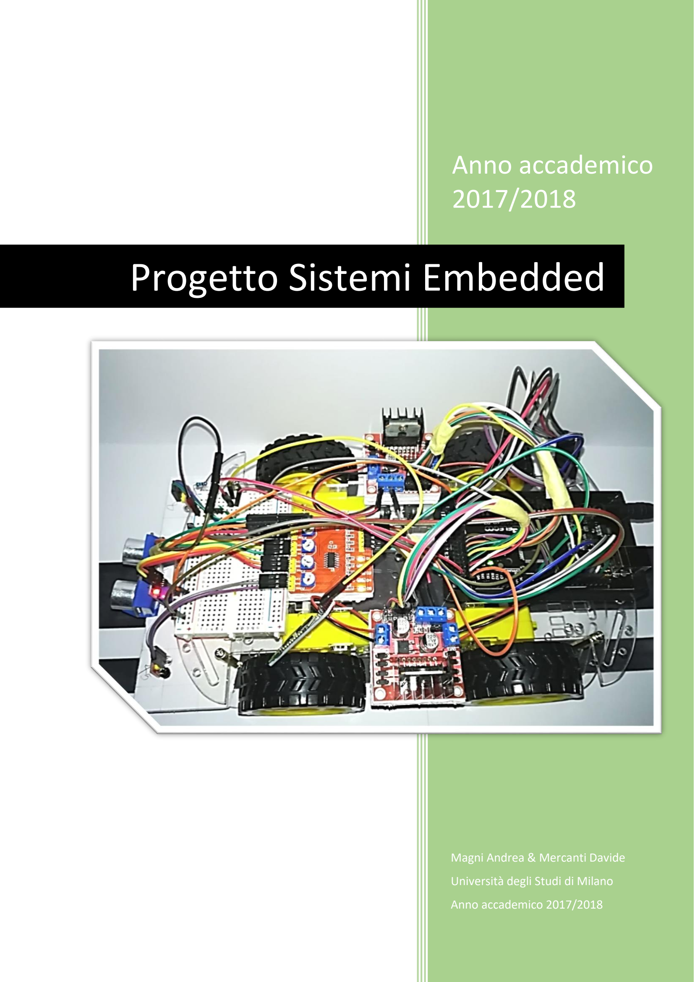
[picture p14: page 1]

# Progetto Sistemi Embedded

Magni Andrea & Mercanti Davide

Università degli Studi di Milano

Anno accademico 2017/2018

Anno accademico 2017/2018 | Sistemi Embedded | Magni Andrea & Mercanti Davide
1 | P a g .

# BREVE DESCRIZIONE

Il progetto che abbiamo deciso di realizzare prevede la costruzione di una "macchina intelligente".

La macchina andrà a svolgere diverse funzioni, principalmente di comunicazione o di valutazione e risoluzione di problematiche, tra le quali:

- riuscire a muoversi all'interno di una strada composta da due corsie, rimanendo all'interno di una corsia
- riuscire ad effettuare una manovra di cambio corsia
- valutare la presenza di un semaforo
- nel caso in cui venga rilevato un semaforo valuti la sua condizione e regoli la velocità di conseguenza
- valutare la presenza di possibili ostacoli durante il percorso
- nel caso in cui venga rilevato un ostacolo valuti il tipo di ostacolo (mobile o fisso) e decida se continuare il percorso o effettuare una manovra di cambio corsia
- comunicare con un telefono per permettere lo scambio di informazioni o ricezione di comandi tra la macchina e l'utente in diretta

# ELENCO COMPONENTI

Quantità | Componente | Link Amazon
1 | Board Arduino Mega | https://www.amazon.it/dp/B06XRJNB27/
1 | Board generica (non sono necessari molti GPIO) | https://www.amazon.it/dp/B01MRJR8UF/
1 | Kit telaio ruote motori | https://www.amazon.it/dp/B073169GBF/
2 | Modulo gestione motori - L298N | https://www.amazon.it/dp/B013QTC18K/
2 | Modulo radio - nRF24L01 | https://www.amazon.it/dp/B016BAPC0K/
1 | Modulo Bluetooth - HC-05 | https://www.amazon.it/dp/B01G9KSAF6/
4 | Sensore ad infrarossi - TE174 o FC-35 | https://www.amazon.it/dp/B00XXEJD58/
3 | Sensore ad ultrasuoni - HC-SR04 | https://www.amazon.it/dp/B00R2U8HK6/
1 | Resistenza 8.2 ohm

https://www.amazon.it/dp/B00J02WSFE/

3 | Resistenza 220 ohm
1 | Resistenza 1 Kohm
1 | Resistenza 2.2 Kohm
1 | Resistenza 10 Kohm
2 | Breadboard | https://www.amazon.it/dp/B06XRDRT2R/
1 | Cavetteria | https://www.amazon.it/dp/B01N40EK6M/
| Polistirolo cartonato

# DESCRIZIONE COMPONENTI UTILIZZATI

Per la creazione di questo progetto sono stati utilizzati diversi componenti, aggiungendo sempre più funzionalità e potendo così testare il funzionamento di diversi sensori e moduli con relative interazioni all’interno di un singolo progetto.

Andremo ora ad analizzare i principali componenti utilizzati all’interno del progetto:

### Telaio / Motori / Ruote

Per la realizzazione di questo progetto o simili è sicuramente fondamentale una scocca che permetta alla macchina di sostenere i vari componenti e successivamente, una volta realizzato il codice e inseriti i vari sensori e moduli, potersi muovere liberamente o all’interno di un tracciato.

Sicuramente la scocca nello specifico è un componente il cui acquisto non risulta
strettamente necessario (sarebbe stato possibile crearlo attraverso del cartone),
avendo però la necessità di comprare delle ruote e relativi motori a corrente continua la differenza di costo tra il comprare un kit telaio/motori/ruote oppure delle ruote e motori singolarmente era irrisoria se non addirittura più conveniente. Abbiamo quindi optato per questo kit con telaio realizzato in plexiglass. I motori presenti nel kit sono
dei comunissimi motori a corrente continua ai quali è possibile fornire una tensione
massima di 6 Volt. Le ruote sono un mix di plastica e gomma.

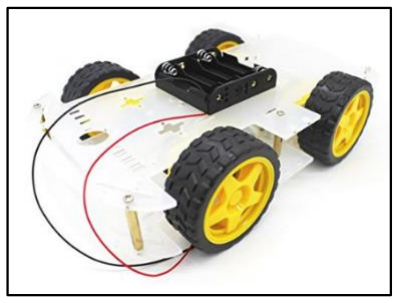
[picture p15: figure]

Per quanto questo kit abbia comportato grandi comodità, bisogna anche dire che i motori non sono particolarmente precisi. Questo lato negativo è evidente durante la guida automatica della macchina, la quale presenta piccole imprecisioni che possono essere notate durante il suo percorso e sono dovute alla non perfetta taratura dei motori. La comodità portata dal kit unita al costo irrisorio ne fanno un acquisto decisamente sensato per il progetto.

### Modulo L298N

Questo modulo è sicuramente un acquisto necessario quando si vuole realizzare un progetto di questo genere.

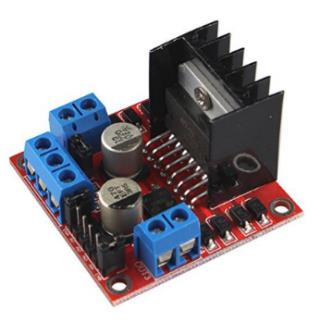
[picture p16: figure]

Il modulo L298N è utilizzato per comandare fino ad un massimo di due motori a corrente continua (o di altro genere), può funzionare con tensioni che variano dai 5 ai 35 Volt e fornire sino a 2 Ampere di corrente per ogni uscita. Particolarmente utile la presenza di un’uscita stabile a 5 Volt, la quale può essere utilizzata per alimentare Arduino, dei componenti oppure per far passare 5 Volt sulla breadboard.

Per il progetto sono stati utilizzati due di questi componenti, potendo così gestire singolarmente ogni motore. Questa soluzione non è necessaria in quanto si potrebbe utilizzare un solo modulo collegando in parallelo a coppie i motori.

### Modulo nRF24L01

Questo modulo viene utilizzato per creare un canale radio attraverso il quale comunicare. Esso non è necessario nel momento in cui si voglia costruire un semplice line follower, può invece risultare molto utile nel momento in cui si ha la necessità di comunicare con altri componenti (ad esempio un radiocomando per controllare la macchina).

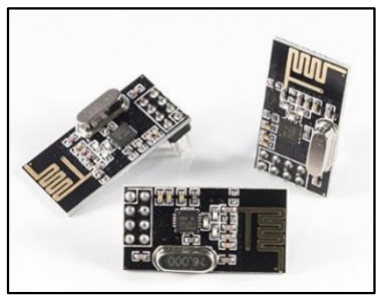
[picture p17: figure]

All’interno del progetto è stato inserito per permettere la comunicazione con un
secondo Arduino, all’interno del quale è caricato un programma che simula un
semaforo.

Il semaforo e la macchina potranno quindi comunicare tra loro, nello specifico sarà il semaforo che invierà alla macchina il suo stato, la macchina andrà ad analizzare lo stato corrente e valuterà come comportarsi.

### Modulo HC-05

Questo modulo permette di gestire una comunicazione tramite Bluetooth e non è sicuramente un acquisto necessario per il progetto dato che un’eventuale connessione tra Arduino e un secondo Arduino è già permessa dal modulo radio.

La scelta di aggiungere questo modulo è stata fatta per due motivi, il principale è quello di poter comunicare con un telefono tramite una delle tante applicazioni presenti sugli store e poter così effettuare un debug in live, molto utile per determinare problemi nel comportamento della macchina in fase di progettazione. In precedenza al posto del Bluetooth era presente un display LCD sul quale erano visualizzate le informazioni. Il secondo motivo per cui ci siamo interessati a questo componente è la possibilità di avere una connessione senza fili con un PC con cui scambiare dati nel caso di futuri sviluppi del progetto, come ad esempio delle applicazioni con Processing per visualizzare il movimento della macchina in live.

### Sensore HC-SR04

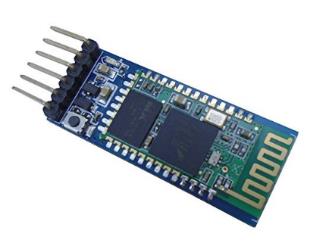
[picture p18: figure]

Questo sensore permette di valutare la distanza tra esso ed un oggetto posto di fronte a lui tramite l’utilizzo degli ultrasuoni. Componente sicuramente interessante per i progetti in cui si interagisce con l’ambiente circostante.

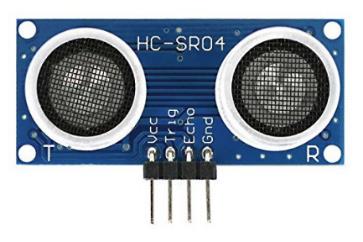
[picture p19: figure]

Trova un doppio utilizzo all’interno del progetto poiché risulta utile sia per la macchina
che per il semaforo. Per la macchina la sua funzione è quella di permettere la
valutazione della presenza di eventuali ostacoli di fronte al suo percorso, per quanto
riguarda il semaforo invece il suo utilizzo è quello di creare una zona di apertura e una di chiusura di invio del segnale radio, evitando così l’invio continuo di dati tra il semaforo e la macchina che potrebbero portare a situazioni indesiderate (la macchina che si ferma lontano dal semaforo).

### Sensore FC-35 / FC-51

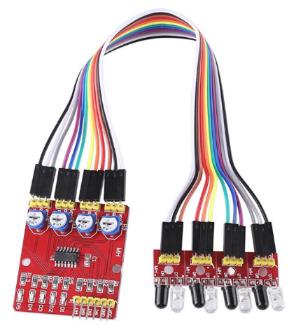
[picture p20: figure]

Questo modulo ad infrarossi viene utilizzato per creare permettere alla macchina di seguire un percorso. Il funzionamento del modulo è molto semplice, è presente un led la cui funzione è quella di trasmettitore ed un fotodiodo o fototransistor che funziona come ricevitore. Il trasmettitore IR invia un segnale infrarosso che, nel caso di una superficie riflettente (ad esempio di colore bianco),

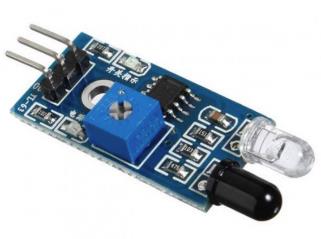
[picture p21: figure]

rimbalza in alcune direzioni compresa quella del ricevitore IR il quale cattura il segnale rilevando l’oggetto. Nel caso di una superficie assorbente (ad esempio di colore nero) il segnale IR non è riflesso e l’oggetto non può essere rilevato dal sensore. Questo risultato si verificherebbe anche se l’oggetto è assente.

### Componentistica varia

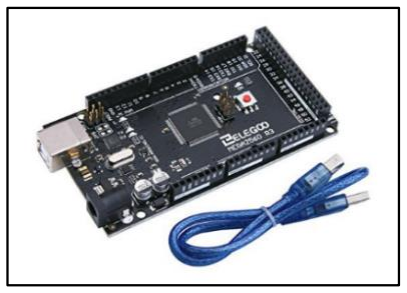
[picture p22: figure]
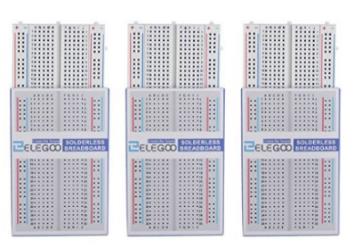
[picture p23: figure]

Per concludere, gli altri componenti utilizzati per il progetto sono una piattaforma Arduino Mega e relativa breadboard per comandare i vari moduli e sensori della macchina, un secondo Arduino Mega con breadboard per creare il semaforo. Inoltre è stata usata molta cavetteria, delle resistenze, dei led per mostrare lo stato del semaforo, due pile 18650 da 3.7 Volt e due pile da 9 Volt per alimentare i due Arduino.

# FOTO

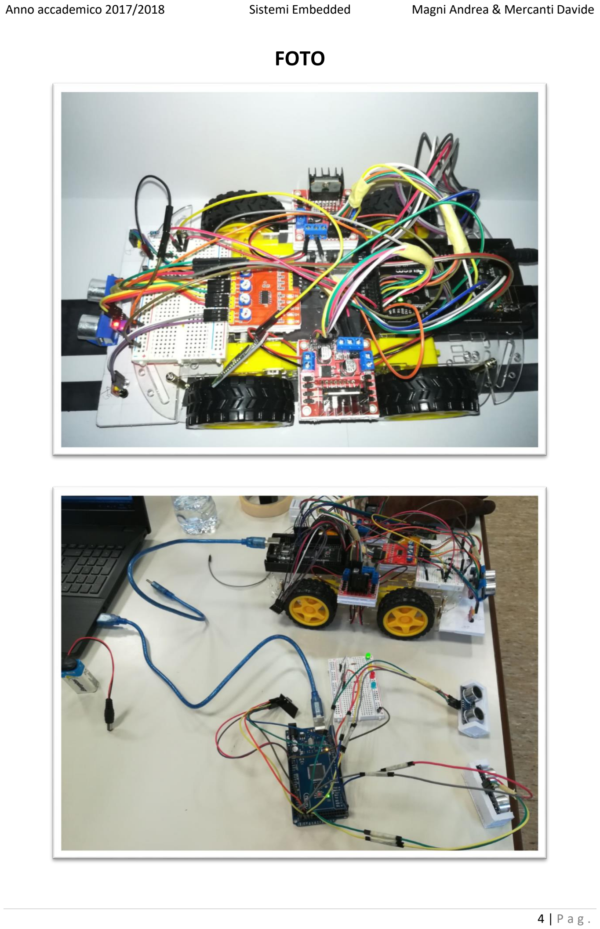
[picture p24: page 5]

# SCHEMA COLLEGAMENTI MACCHINA

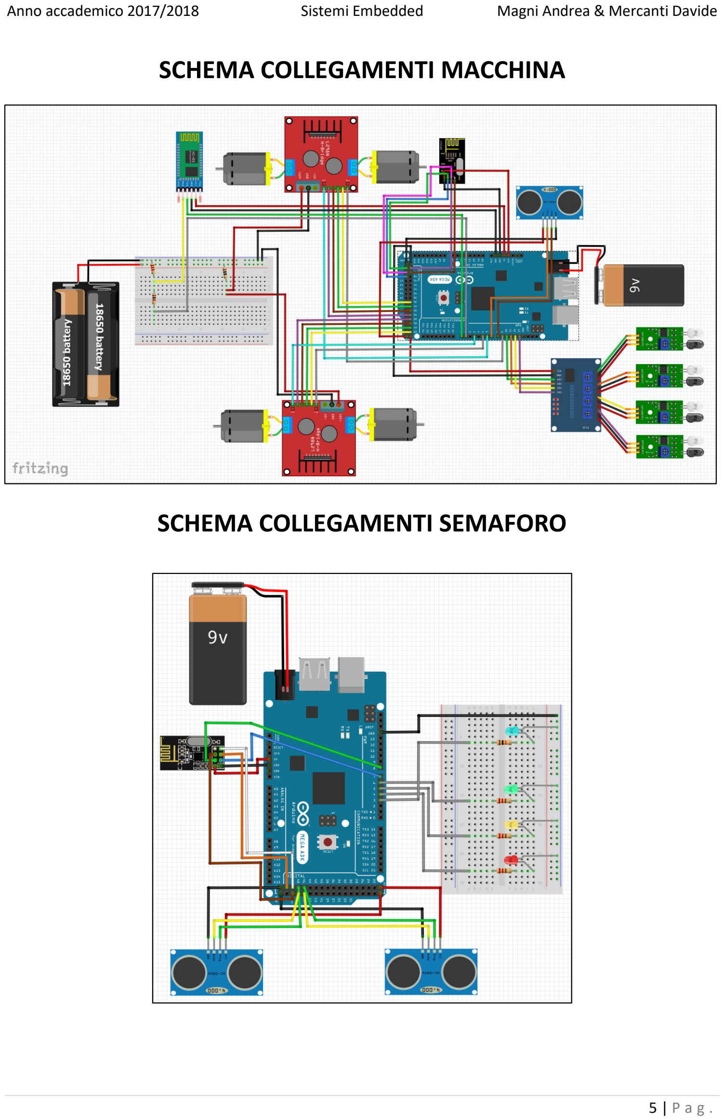
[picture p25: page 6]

# SCHEMA COLLEGAMENTI SEMAFORO

# POSSIBILI UPGRADE

- Realizzazione di un sistema di semafori, ad esempio un incrocio, il quale valuti la presenza di cose di macchine nelle varie strade e decida come impostare i semafori in modo intelligente.
- Realizzazione di un sistema GPS per tenere traccia degli spostamenti della macchina, probabilmente sulla piccola scala dei movimenti della macchina potrebbe essere difficile o inutile da sviluppare ma potrebbe portare ad idee alternative collegate.
- Realizzazione di un collegamento tra la macchina e Processing scrivendo del codice per ricreare il tracciato percorso dalla macchina durante ogni sessione di utilizzo.
- Realizzazione di un sistema di sterzo per permettere alla macchina di curvare.
- Realizzazione di un sonar mobile, creato unendo un sensore ad ultrasuoni ad un servomotore. In questo modo sarebbe possibile analizzare le distanze degli oggetti non solo se frontali rispetto al modulo ad ultrasuoni ma anche attorno ad esso.

# COLLEGAMENTO MACCHINA - SMARTPHONE

Il progetto ha la possibilità di interfacciarsi ad una periferica che supporta il collegamento Bluetooth, personalmente abbiamo testato le funzionalità del progetto grazie a questa applicazione presente sullo store Android: https://play.google.com/store/apps/details?id=com.giumig.apps.bluetoothserialmonitor&hl=it

Non sono garantite compatibilità con altre applicazioni dato che per il momento non abbiamo avuto modo di effettuare test multipli.

Nel momento in cui si voglia stabilire una connessione con la macchina, dopo aver installato ed aperto l’applicazione dovrebbe comparare il dispositivo HC-05. Selezionarlo ed inserire come key 1234 nel caso in cui sia richiesta. A questo punto avrete una connessione attiva tra macchina e smartphone.

Il telefono può inviare determinati comandi premendo i seguenti numeri:

### 1 Visualizzazione comandi

### 2 Attivazione debug

### 3 Disattivazione debug

### 4 Aumento potenza motori

### 5 Riduzione potenza motori

### 6 Attivazione controllo manuale

### 7 Disattivazione controllo manuale

### 8 Attivazione modalità standby

### 9 Disattivazione modalità standby

Per utilizzare i comandi manuali uscire interfacciarsi al modulo Bluetooth come Joystick invece che come terminale e usare i seguenti tasti:

W Per andare in avanti
A Per andare a sinistra
D Per andare a destra
S Per andare in retro
Z Per fermare la macchina
Q Per uscire dalla modalità manuale impostando lo standby

# CODICE REALIZZATO

Per la realizzazione di questo progetto sono stati creati principalmente quattro file:
- macchina.ino per la gestione della macchina
- semaforo.ino per la gestione del semaforo
- motor.h e motor.cpp una libreria creata appositamente per il progetto
Inoltre sono in fase di testing ulteriori file / funzioni che non siamo ancora riusciti ad implementare al 100% al momento della stesura della relazione ma verranno comunque integrati successivamente.

/*
* Nome file: macchina.ino
*
* Questo programma permette alla macchina, attraverso diverse funzioni, sensori e moduli di poter valutare * ed interagire con l’esterno. Nello specifico la macchina dovrà riuscire a muoversi all’interno di una strada
* appositamente creata e comunicare attraverso segnali Bluetooth e Radio con altri oggetti.
*
* Informazioni dettagliate sul progetto al seguente link: https://github.com/AndreaMagni/SistemiEmbedded/*
* Copyright © 2018, Magni Andrea & Mercanti Davide, 23 Febbraio 2018
*
* This program is free software: you can redistribute it and/or modify it under the terms of the GNU General
* Public License as published by the Free Software Foundation, either version 3 of the License, or (at your option) * any later version.
*
* This program is distributed in the hope that it will be useful, but WITHOUT ANY WARRANTY; without even the * implied warranty of MERCHANTABILITY or FITNESS FOR A PARTICULAR PURPOSE. See the GNU General Public * License for more details.
*
* You should have received a copy of the GNU General Public License with this program.
* If not, see <http://www.gnu.org/licenses/>.
*/

/*
* Inclusione librerie necessarie per il funzionamento del programma
*
* NewPing.h utilizzata per la gestione del sensore ad ultrasuoni
* SPI.h utilizzata per la comunicazione con dispositivi SPI (Serial Peripheral Interface) * RF24.h utilizzata per la gestione del modulo radio
* Motor.h creata per semplificare l’utilizzo dei motori
*/

#include <NewPing.h>

#include <SPI.h>

#include <RF24.h>

#include "Motor.h"

/*
* Definizione etichette per i sensori ad infrarossi
* nessun ostacolo rilevato [1] - ostacolo rilevato [0] *
* DETECT_ED - Sensore esterno destro
* DETECT_CD - Sensore centrale destro
* DETECT_CS - Sensore centrale sinistro * DETECT_ES - Sensore esterno sinistro */

#define DETECT_ED 10

#define DETECT_CD 11

#define DETECT_CS 12

#define DETECT_ES 13

/*
* Dichiarazione e assegnazione di diverse variabili
*
* turn_left: stato della macchina "cambio corsia verso sinistra" * turn_right: stato della macchina "cambio corsia verso destra"
* debug: stato debug della macchina (attivo / disattivo)
* standby: stato standby della macchina (attivo / disattivo)
* manual: stato comandi manuali della macchina (attivo / disattivo)
* command: determina il comando da eseguire tramite Bluetooth
* received_loop: determina l'ultimo loop ricevuto dal semaforo
* max_acceptable_loop: determina il massimo loop accettabile oltre il quale la
* | macchina valuta il semaforo giallo come se fosse rosso
* motor_power_plus: determina la quantità di potenza aggiunta via Bluetooth ai motori * motor_power_minus: determina la quantità di potenza tolta via Bluetooth ai motori * motor_power_difference: differenza tra motor_power_plus e motor_power_minus * set_delay: imposta il delay dopo l'invio di un messaggio del menù Bluetooth
* obstacle_distance: imposta la distanza sotto la quale viene rilevato un ostacolo
* pipe: definisce l’indirizzo di comunicazione radio
* channel: definisce il channel nell’indirizzo di comunicazione radio
*/

bool turn_left = false;
bool turn_right = false;
bool debug = false;
bool standby = false;
bool manual = false
int command = 0;
int received_loop;
int max_acceptable_loop = 75; int motor_power_plus = 0;
int motor_power_minus = 0; int motor_power_difference = 0; int set_delay = 1000;
int obstacle_distance = 15;

const uint64_t pipe = 0xABCDEF; // unsigned long long const uint8_t channel = 0x1; // unsigned char

/*
* Creazione oggetti
*
* sonar(trigger_pin, echo_pin, max_cm_distance)
* Sensore ad ultrasuoni utilizzato per le rilevazioni delle distanza
*
* mt(speed_[m1, m2, m3, m4], dir_a_[m1, m2, m3, m4], dir_b_[m1, m2, m3, m4]) * Gestione dei quattro motori, velocità e verso, in un singolo oggetto
*
* radio(ce, csn)
* Modulo radio per la comunicazione con il semaforo
*/

NewPing sonar(7, 8, 200);
Motor mt(5, 3, 9, 6, 22, 26, 30, 34, 24, 28, 32, 36); RF24 radio(49, 53);

/*
* Funzione secureDigitalRead(int pin)
*
* Questa funzione è stata creata per avere più sicurezza sui dati letti * da parte dei sensori ad infrarossi. Essi a volte risultano imprecisi e * quindi è stato inserito un controllo.
*/

bool secureDigitalRead(int pin) {
bool register tmp1, tmp2, tmp3; tmp1 = digitalRead(pin);
delay(1);
tmp2 = digitalRead(pin);
delay(1);
tmp3 = digitalRead(pin);
return (tmp1&&tmp2) || (tmp2&&tmp3) || (tmp1&&tmp3); }

/*
* Funzione obstacleDetection()
*
* La funzione permette alla macchina di determinare se è presente un * ostacolo entro una quantità di centimetri specificata in precedenza * nella variabile obstacle_distance
*/

bool obstacleDetection() {
int pingTime = sonar.ping_median(3);
int distance = sonar.convert_cm(pingTime);

if (distance <= obstacle_distance) {
if (debug) {
Serial.print(" Ostacolo rilevato entro "); Serial.print(distance);
Serial.println(" cm");
}
return true;
}
else return false;
}

/* Funzione light_status()
*
* La funzione permette alla macchina di determinare lo stato del semaforo * tramite la ricezione di dati via segnale radio. Una volta ricevuti i
* dati vengono elaborati, nel caso in cui il semaforo sia rosso oppure
* sia giallo verso la fine la macchina si ferma. Nel resto dei casi
* la macchina continua il tragitto
*/

bool light_status() {

if (radio.available()) {
char received_status[7] = "";
radio.read(&received_status, sizeof(received_status));
if (strncmp(received_status, "001",3) == 0) {
if (debug) Serial.println(" Semaforo rosso - Macchina ferma"); return false;
} else if (strncmp(received_status, "010",3) == 0) {
received_loop = received_status[4];
if (received_loop >= max_acceptable_loop) {
if (debug) {Serial.println(" Semaforo giallo - Macchina ferma loop "); Serial.println(received_loop);} return false;
} else {
return true;
}
} else {
return true;
}
}

}

/* Setup */

void setup() {

Serial.begin(9600);
pinMode(DETECT_ED,INPUT);

pinMode(DETECT_CD,INPUT);
pinMode(DETECT_CS,INPUT);
pinMode(DETECT_ES,INPUT);
radio.begin();
radio.setChannel(channel); radio.openReadingPipe(0, pipe); radio.setPALevel(RF24_PA_MIN); radio.startListening();

}

/* Loop */

void loop() {

if (!manual) {

while (Serial.available() > 0){

command = Serial.read();

switch (command) {

case '1':
Serial.println(" Elenco comandi disponibili:"); Serial.println("");
Serial.println(" 1 - Visualizzazione comandi"); Serial.println(" 2 - Attivazione debug"); Serial.println(" 3 - Disattivazione debug"); Serial.println(" 4 - Aumento potenza motori"); Serial.println(" 5 - Riduzione potenza motori"); Serial.println(" 6 - Attivazione controllo manuale"); Serial.println(" 7 - Disattivazione controllo manuale"); Serial.println(" 8 - Attivazione modalità standby"); Serial.println(" 9 - Disattivazione modalità standby"); Serial.println("");
for (int i = 30; i >= 1; i--) {
if (i%10 == 0) {
Serial.print(" Disconnessione menù in "); Serial.print(i);
Serial.println(" secondi");
delay(1000);
} else if (i == 1) {
Serial.println(" Disconnessione riuscita"); delay(1000);
}
}
break;

case '2':
Serial.println(" 2 | Attivazione debug");
debug = true;
delay(set_delay);
break;

case '3':
Serial.println(" 3 | Disattivazione debug");
debug = false;
delay(set_delay);
break;

case '4':
Serial.println(" 4 | Aumento potenza motori");
Serial.println("");
Serial.println(" Attualmente la potenza dei motori");
Serial.print(" differisce dai valori originali per ");
motor_power_plus += 5;
motor_power_difference = motor_power_plus - motor_power_minus; Serial.println(motor_power_difference);
delay(set_delay);
break;

case '5':
Serial.println(" 5 | Riduzione potenza motori");
Serial.println("");
Serial.println(" Attualmente la potenza dei motori");
Serial.print(" differisce dai valori originali per ");
motor_power_minus += 5;
motor_power_difference = motor_power_plus - motor_power_minus; Serial.println(motor_power_difference);
delay(set_delay);
break;

case '6':
Serial.println(" 6 | Attivazione controllo manuale");
manual = true;
delay(set_delay);
break;

case '7':
Serial.println(" 7 | Disattivazione controllo manuale");
manual = false;
delay(set_delay);
break;

case '8':
Serial.println(" 8 | Attivazione modalità standby");
standby = true;

delay(set_delay);
break;

case '9':
Serial.println(" 9 | Disattivazione modalità standby");
standby = false;
delay(set_delay);
break;

default:
Serial.println(" Comando non riconosciuto"); Serial.println("");
Serial.println(" Premere 1 per visualizzare i comandi"); delay(set_delay);
break;

}

}

}

if (standby) {

mt.car_stop();
Serial.println(" STANDBY ATTIVO"); Serial.println("");
Serial.println(" Premere 9 per disattivare"); Serial.println("");
delay(3000);

} else {

if (manual) {

while (Serial.available() > 0){

command = Serial.read();

switch (command) {

case 'W':
mt.car_forward(80 + motor_power_difference); //delay(300);
break;

case 'A':
mt.car_left(125 + motor_power_difference); //delay(300);

break;

case 'S':
mt.car_backward(80 + motor_power_difference); //delay(300);
break;

case 'D':
mt.car_right(125 + motor_power_difference); //delay(300);
break;

case 'Q':
manual = false;
standby = true;
command = 0;
break;

default:
mt.car_stop();
break;

}

}

} else {

if (!light_status()) {

mt.car_stop();
if (debug) {Serial.println(" ATTENZIONE: stop per il semaforo");}

} else {

if (obstacleDetection() && !turn_left && secureDigitalRead(DETECT_ED) && secureDigitalRead(DETECT_CD) && secureDigitalRead(DETECT_CS)) {
mt.car_stop();
if (debug) {Serial.println(" Valutazione ostacolo in corso. Attendere 5 secondi");}
delay(5000);
if (obstacleDetection()) {
if (debug) {Serial.println(" Ostacolo fisso. Manovra di cambio corsia in corso"); delay(1000);} turn_left = true;
if (debug) {Serial.println(" Manovra: c.c. retro D -> S");}
mt.car_backward(80);
delay(500);
if (debug) {Serial.println(" Manovra: c.c. sinistra D -> S");} mt.car_left(220);
delay(800);
} else {

if (debug) {Serial.println(" Ostacolo mobile. Rimanere nella stessa corsia"); delay(1000);}
}

} else if (obstacleDetection() && !turn_right && secureDigitalRead(DETECT_ES) && secureDigitalRead(DETECT_CD) && secureDigitalRead(DETECT_CS)) {

mt.car_stop();
if (debug) {Serial.println(" Valutazione ostacolo in corso. Attendere 5 secondi");} delay(5000);
if (obstacleDetection()) {
if (debug) {Serial.println(" Ostacolo fisso. Manovra di cambio corsia in corso"); delay(1000);} turn_right = true;
if (debug) {Serial.println(" Manovra: c.c. retro S -> D");}
mt.car_backward(80);
delay(500);
if (debug) {Serial.println(" Manovra: c.c. destra S -> D");} mt.car_right(220);
delay(800);
} else {
if (debug) {Serial.println(" Ostacolo mobile. Rimanere nella stessa corsia"); delay(1000);} }

}

if (turn_left) {
if (secureDigitalRead(DETECT_CD)) {
turn_left = false;
while (secureDigitalRead(DETECT_CD) && !(secureDigitalRead(DETECT_CS))) { mt.car_right(140);
if (debug) {Serial.println(" Manovra: c.c. allineamento");}
}
} else {
mt.car_forward(75);
if (debug) {Serial.println(" Manovra: c.c. avanti D -> S");} }
} else if (turn_right) {
if (secureDigitalRead(DETECT_CS)) {
turn_right = false;
while (secureDigitalRead(DETECT_CS) && !(secureDigitalRead(DETECT_CD))) { mt.car_left(140);
if (debug) {Serial.println(" Manovra: c.c. allineamento");}
}
} else {
mt.car_forward(75);
if (debug) {Serial.println(" Manovra: c.c. avanti S -> D");} }
} else {
if (digitalRead(DETECT_CD) && digitalRead(DETECT_CS)) { if (debug) {Serial.println(" Manovra: avanti");} mt.car_forward(70 + motor_power_difference);

} else if (!(digitalRead(DETECT_CD)) && digitalRead(DETECT_CS)) { if (debug) {Serial.println(" Manovra: sinistra");}
mt.car_left(110 + motor_power_difference);
} else if (digitalRead(DETECT_CD) && !(digitalRead(DETECT_CS))) { if (debug) {Serial.println(" Manovra: destra");}
mt.car_right(110 + motor_power_difference);
} else if (!(digitalRead(DETECT_CD)) && !(digitalRead(DETECT_CS))) { if (debug) {Serial.println(" Manovra: stop");}
mt.car_stop();
}
}
}

if (debug) {Serial.println("-----------------------------------------------------------");}

}

}

}

/*
* Nome file: semaforo.ino
*
* Questo programma permette al semaforo di valutare la presenza di una macchina all'interno di un determinato range * stabilito dalla presenza di due sensori ad ultrasuoni. Quando la macchina supera il primo sensore viene attivato
* il canale radio e lo stato del semaforo viene comunicato alla macchina. Il programma è stato creato per permettere * una distinzione del semaforo giallo tramite la variabile loopTime, la quale permette di valutare se il giallo è
* appena iniziato e quindi la macchina può proseguire oppure è quasi finito e la macchina deve fermarsi.
*
* Informazioni dettagliate sul progetto al seguente link: https://github.com/AndreaMagni/SistemiEmbedded/*
* Copyright © 2018, Magni Andrea & Mercanti Davide, 23 Febbraio 2018
*
* This program is free software: you can redistribute it and/or modify it under the terms of the GNU General
* Public License as published by the Free Software Foundation, either version 3 of the License, or (at your option) * any later version.
*
* This program is distributed in the hope that it will be useful, but WITHOUT ANY WARRANTY; without even the * implied warranty of MERCHANTABILITY or FITNESS FOR A PARTICULAR PURPOSE. See the GNU General Public * License for more details.
*
* You should have received a copy of the GNU General Public License with this program.
* If not, see <http://www.gnu.org/licenses/>.
*/

/* Inclusione librerie */

#include <NewPing.h>

#include <SPI.h>

#include <RF24.h>

/* Definizione etichette per i LED */

#define RED_LED 4

#define YELLOW_RED 5

#define GREEN_LED 6

/* Creazione oggetti */

RF24 radio(7, 8);
NewPing sonarA(46, 47, 500);
NewPing sonarB(49, 48, 500);

/* Dichiarazione e assegnazione variabili */
/* multiplier 50 corrisponde più o meno a 10 secondi */

bool debug = 1;
bool car_presence = false;
int loop_time;
int loop_time_multiplier = 50; int max_distance = 25;
const uint64_t pipe = 0xABCDEF; const uint8_t channel = 0x1;

/* Setup */

void setup() {

Serial.begin(9600);
pinMode(GREEN_LED, OUTPUT); pinMode(YELLOW_RED, OUTPUT); pinMode(RED_LED, OUTPUT);
radio.begin();

radio.setChannel(channel); radio.openWritingPipe(pipe); radio.setPALevel(RF24_PA_MIN); radio.stopListening();

}

/* Loop */

void loop() {

loop_time = 0;

for (loop_time; loop_time <= loop_time_multiplier*1; loop_time++) { green_light();
if (debug) {Serial.print("Loop time = "); Serial.println(loop_time);} if (car_presence) light_status();
}

for (loop_time; loop_time <= loop_time_multiplier*2; loop_time++) { yellow_light();
if (debug) {Serial.print("Loop time = "); Serial.println(loop_time);} if (car_presence) light_status();
}

for (loop_time; loop_time <= loop_time_multiplier*3; loop_time++) { red_light();
if (debug) {Serial.print("Loop time = "); Serial.println(loop_time);} if (car_presence) light_status();
}

}

/* Funzione obstacle_detection_A */

bool obstacle_detection_A() {

int ping_time = sonarA.ping_median(3);
int distance = sonarA.convert_cm(ping_time);
if (debug) {Serial.print("Distanza ostacolo A - "); Serial.println(distance);} if (distance <= max_distance) return true;
else return false;

}

/* Funzione detected_A */

void detected_A() {

if (debug) Serial.println("Trovato ostacolo A - Settaggio car a true"); car_presence = true;

}

/* Funzione obstacle_detection_B */

bool obstacle_detection_B() {

int ping_time = sonarB.ping_median(3);
int distance = sonarB.convert_cm(ping_time);
if (debug) {Serial.print("Distanza ostacolo B - "); Serial.println(distance);} if (distance <= max_distance) return true;
else return false;

}

/* Funzione detected_B */

void detected_B() {

if (debug) Serial.println("Trovato ostacolo B - Settaggio car a false"); car_presence = false;

}

/* Funzione light_status */

void light_status() {

int green_status = digitalRead(GREEN_LED); int yellow_status = digitalRead(YELLOW_RED);
int red_status = digitalRead(RED_LED);
char actual_status[7];
sprintf(actual_status, "%d%d%d,%c", green_status, yellow_status, red_status, (char)loop_time); radio.write(&actual_status, sizeof(actual_status));
if (debug) {Serial.print("Dati inviati: "); Serial.println(actual_status); Serial.println("-------------------------------");}

}

/* Funzione green_light */

void green_light() {

digitalWrite(GREEN_LED, HIGH); digitalWrite(YELLOW_RED, LOW); digitalWrite(RED_LED, LOW);
if (obstacle_detection_A()) detected_A();
if (obstacle_detection_B()) detected_B();
if (debug) {Serial.println("Stato semaforo attuale: VERDE"); Serial.print("Trasmissione: "); Serial.println(car_presence);}

}

/* Funzione yellow_light */

void yellow_light() {

digitalWrite(GREEN_LED, LOW); digitalWrite(YELLOW_RED, HIGH); digitalWrite(RED_LED, LOW);
if (obstacle_detection_A()) detected_A();
if (obstacle_detection_B()) detected_B();
if (debug) {Serial.println("Stato semaforo attuale: GIALLO"); Serial.print("Trasmissione: "); Serial.println(car_presence);}

}

/* Funzione red_light */

void red_light() {

digitalWrite(GREEN_LED, LOW); digitalWrite(YELLOW_RED, LOW); digitalWrite(RED_LED, HIGH);
if (obstacle_detection_A()) detected_A();
if (obstacle_detection_B()) detected_B();
if (debug) {Serial.println("Stato semaforo attuale: ROSSO"); Serial.print("Trasmissione: "); Serial.println(car_presence);}

}

/*
* Nome file: Motor.h
*
* Libreria creata per gestire i motori
*
* Informazioni dettagliate al seguente link: https://github.com/AndreaMagni/SistemiEmbedded/*
* Copyright © 2018, Magni Andrea & Mercanti Davide, 23 Febbraio 2018
*
* This program is free software: you can redistribute it and/or modify it under the terms of the GNU General
* Public License as published by the Free Software Foundation, either version 3 of the License, or (at your option) * any later version.
*
* This program is distributed in the hope that it will be useful, but WITHOUT ANY WARRANTY; without even the * implied warranty of MERCHANTABILITY or FITNESS FOR A PARTICULAR PURPOSE. See the GNU General Public * License for more details.
*
* You should have received a copy of the GNU General Public License with this program.
* If not, see <http://www.gnu.org/licenses/>.
*/

#ifndef Motor_h

#define Motor_h

#include "Arduino.h"

class Motor {
public:
Motor(int PIN_SPEED_M1, int PIN_SPEED_M2, int PIN_SPEED_M3, int PIN_SPEED_M4, int PIN_DIR_A_M1, int PIN_DIR_A_M2, int PIN_DIR_A_M3, int PIN_DIR_A_M4, int PIN_DIR_B_M1, int PIN_DIR_B_M2, int PIN_DIR_B_M3, int PIN_DIR_B_M4);
void car_forward(int SPEED);
void car_backward(int SPEED);
void car_left(int SPEED);
void car_right(int SPEED);
void car_forward(int SPEED_1, int SPEED_2, int SPEED_3, int SPEED_4); void car_backward(int SPEED_1, int SPEED_2, int SPEED_3, int SPEED_4); void car_left(int SPEED_1, int SPEED_2, int SPEED_3, int SPEED_4);
void car_right(int SPEED_1, int SPEED_2, int SPEED_3, int SPEED_4); void car_stop();
private:
int _PIN_SPEED_M1;
int _PIN_SPEED_M2;
int _PIN_SPEED_M3;
int _PIN_SPEED_M4;
int _PIN_DIR_A_M1;
int _PIN_DIR_A_M2;
int _PIN_DIR_A_M3;
int _PIN_DIR_A_M4;
int _PIN_DIR_B_M1;
int _PIN_DIR_B_M2;
int _PIN_DIR_B_M3;
int _PIN_DIR_B_M4;
};

#endif

/*
* Nome file: Motor.cpp
*
* Libreria creata per gestire i motori
*
* Informazioni dettagliate al seguente link: https://github.com/AndreaMagni/SistemiEmbedded/*
* Copyright © 2018, Magni Andrea & Mercanti Davide, 23 Febbraio 2018
*
* This program is free software: you can redistribute it and/or modify it under the terms of the GNU General
* Public License as published by the Free Software Foundation, either version 3 of the License, or (at your option) * any later version.
*
* This program is distributed in the hope that it will be useful, but WITHOUT ANY WARRANTY; without even the * implied warranty of MERCHANTABILITY or FITNESS FOR A PARTICULAR PURPOSE. See the GNU General Public * License for more details.
*
* You should have received a copy of the GNU General Public License with this program.
* If not, see <http://www.gnu.org/licenses/>.
*/

#include "Arduino.h"

#include "Motor.h"

Motor::Motor(int PIN_SPEED_M1, int PIN_SPEED_M2, int PIN_SPEED_M3, int PIN_SPEED_M4, int PIN_DIR_A_M1, int PIN_DIR_A_M2, int PIN_DIR_A_M3, int PIN_DIR_A_M4, int PIN_DIR_B_M1, int PIN_DIR_B_M2, int PIN_DIR_B_M3, int PIN_DIR_B_M4) {
pinMode(PIN_SPEED_M1, OUTPUT);
pinMode(PIN_DIR_A_M1, OUTPUT);
pinMode(PIN_DIR_B_M1, OUTPUT); pinMode(PIN_SPEED_M2, OUTPUT); pinMode(PIN_DIR_A_M2, OUTPUT); pinMode(PIN_DIR_B_M2, OUTPUT); pinMode(PIN_SPEED_M3, OUTPUT); pinMode(PIN_DIR_A_M3, OUTPUT); pinMode(PIN_DIR_B_M3, OUTPUT); pinMode(PIN_SPEED_M4, OUTPUT); pinMode(PIN_DIR_A_M4, OUTPUT); pinMode(PIN_DIR_B_M4, OUTPUT); _PIN_SPEED_M1 = PIN_SPEED_M1; _PIN_DIR_A_M1 = PIN_DIR_A_M1; _PIN_DIR_B_M1 = PIN_DIR_B_M1; _PIN_SPEED_M2 = PIN_SPEED_M2; _PIN_DIR_A_M2 = PIN_DIR_A_M2; _PIN_DIR_B_M2 = PIN_DIR_B_M2; _PIN_SPEED_M3 = PIN_SPEED_M3; _PIN_DIR_A_M3 = PIN_DIR_A_M3; _PIN_DIR_B_M3 = PIN_DIR_B_M3; _PIN_SPEED_M4 = PIN_SPEED_M4; _PIN_DIR_A_M4 = PIN_DIR_A_M4; _PIN_DIR_B_M4 = PIN_DIR_B_M4;
}

void Motor::car_forward(int SPEED) { analogWrite(_PIN_SPEED_M1, SPEED); analogWrite(_PIN_SPEED_M2, SPEED); analogWrite(_PIN_SPEED_M3, SPEED); analogWrite(_PIN_SPEED_M4, SPEED); digitalWrite(_PIN_DIR_A_M1, LOW); digitalWrite(_PIN_DIR_B_M1, HIGH); digitalWrite(_PIN_DIR_A_M2, LOW); digitalWrite(_PIN_DIR_B_M2, HIGH); digitalWrite(_PIN_DIR_A_M3, LOW);

digitalWrite(_PIN_DIR_B_M3, HIGH); digitalWrite(_PIN_DIR_A_M4, LOW);
digitalWrite(_PIN_DIR_B_M4, HIGH);
}

void Motor::car_forward(int SPEED_1, int SPEED_2, int SPEED_3, int SPEED_4) { analogWrite(_PIN_SPEED_M1, SPEED_1);
analogWrite(_PIN_SPEED_M2, SPEED_2);
analogWrite(_PIN_SPEED_M3, SPEED_3);
analogWrite(_PIN_SPEED_M4, SPEED_4); digitalWrite(_PIN_DIR_A_M1, LOW); digitalWrite(_PIN_DIR_B_M1, HIGH); digitalWrite(_PIN_DIR_A_M2, LOW); digitalWrite(_PIN_DIR_B_M2, HIGH); digitalWrite(_PIN_DIR_A_M3, LOW); digitalWrite(_PIN_DIR_B_M3, HIGH); digitalWrite(_PIN_DIR_A_M4, LOW); digitalWrite(_PIN_DIR_B_M4, HIGH); }

void Motor::car_backward(int SPEED) { analogWrite(_PIN_SPEED_M1, SPEED); analogWrite(_PIN_SPEED_M2, SPEED); analogWrite(_PIN_SPEED_M3, SPEED); analogWrite(_PIN_SPEED_M4, SPEED); digitalWrite(_PIN_DIR_A_M1, HIGH); digitalWrite(_PIN_DIR_B_M1, LOW); digitalWrite(_PIN_DIR_A_M2, HIGH); digitalWrite(_PIN_DIR_B_M2, LOW); digitalWrite(_PIN_DIR_A_M3, HIGH); digitalWrite(_PIN_DIR_B_M3, LOW); digitalWrite(_PIN_DIR_A_M4, HIGH);
digitalWrite(_PIN_DIR_B_M4, LOW);
}

void Motor::car_backward(int SPEED_1, int SPEED_2, int SPEED_3, int SPEED_4) { analogWrite(_PIN_SPEED_M1, SPEED_1);
analogWrite(_PIN_SPEED_M2, SPEED_2);
analogWrite(_PIN_SPEED_M3, SPEED_3);
analogWrite(_PIN_SPEED_M4, SPEED_4); digitalWrite(_PIN_DIR_A_M1, HIGH); digitalWrite(_PIN_DIR_B_M1, LOW); digitalWrite(_PIN_DIR_A_M2, HIGH); digitalWrite(_PIN_DIR_B_M2, LOW); digitalWrite(_PIN_DIR_A_M3, HIGH); digitalWrite(_PIN_DIR_B_M3, LOW); digitalWrite(_PIN_DIR_A_M4, HIGH); digitalWrite(_PIN_DIR_B_M4, LOW); }

void Motor::car_left(int SPEED) { analogWrite(_PIN_SPEED_M1, SPEED); analogWrite(_PIN_SPEED_M2, SPEED); analogWrite(_PIN_SPEED_M3, SPEED); analogWrite(_PIN_SPEED_M4, SPEED); digitalWrite(_PIN_DIR_A_M1, HIGH); digitalWrite(_PIN_DIR_B_M1, LOW); digitalWrite(_PIN_DIR_A_M2, HIGH); digitalWrite(_PIN_DIR_B_M2, LOW); digitalWrite(_PIN_DIR_A_M3, LOW); digitalWrite(_PIN_DIR_B_M3, HIGH); digitalWrite(_PIN_DIR_A_M4, LOW); digitalWrite(_PIN_DIR_B_M4, HIGH); }

void Motor::car_left(int SPEED_1, int SPEED_2, int SPEED_3, int SPEED_4) { analogWrite(_PIN_SPEED_M1, SPEED_1);
analogWrite(_PIN_SPEED_M2, SPEED_2);
analogWrite(_PIN_SPEED_M3, SPEED_3);
analogWrite(_PIN_SPEED_M4, SPEED_4); digitalWrite(_PIN_DIR_A_M1, HIGH); digitalWrite(_PIN_DIR_B_M1, LOW); digitalWrite(_PIN_DIR_A_M2, HIGH); digitalWrite(_PIN_DIR_B_M2, LOW); digitalWrite(_PIN_DIR_A_M3, LOW); digitalWrite(_PIN_DIR_B_M3, HIGH); digitalWrite(_PIN_DIR_A_M4, LOW); digitalWrite(_PIN_DIR_B_M4, HIGH); }

void Motor::car_right(int SPEED) { analogWrite(_PIN_SPEED_M1, SPEED); analogWrite(_PIN_SPEED_M2, SPEED); analogWrite(_PIN_SPEED_M3, SPEED); analogWrite(_PIN_SPEED_M4, SPEED); digitalWrite(_PIN_DIR_A_M1, LOW); digitalWrite(_PIN_DIR_B_M1, HIGH); digitalWrite(_PIN_DIR_A_M2, LOW); digitalWrite(_PIN_DIR_B_M2, HIGH); digitalWrite(_PIN_DIR_A_M3, HIGH); digitalWrite(_PIN_DIR_B_M3, LOW); digitalWrite(_PIN_DIR_A_M4, HIGH);
digitalWrite(_PIN_DIR_B_M4, LOW);
}

void Motor::car_right(int SPEED_1, int SPEED_2, int SPEED_3, int SPEED_4) { analogWrite(_PIN_SPEED_M1, SPEED_1);
analogWrite(_PIN_SPEED_M2, SPEED_2);
analogWrite(_PIN_SPEED_M3, SPEED_3);
analogWrite(_PIN_SPEED_M4, SPEED_4); digitalWrite(_PIN_DIR_A_M1, LOW); digitalWrite(_PIN_DIR_B_M1, HIGH); digitalWrite(_PIN_DIR_A_M2, LOW); digitalWrite(_PIN_DIR_B_M2, HIGH); digitalWrite(_PIN_DIR_A_M3, HIGH); digitalWrite(_PIN_DIR_B_M3, LOW); digitalWrite(_PIN_DIR_A_M4, HIGH); digitalWrite(_PIN_DIR_B_M4, LOW); }

void Motor::car_stop() {
analogWrite(_PIN_SPEED_M1, 0); analogWrite(_PIN_SPEED_M2, 0); analogWrite(_PIN_SPEED_M3, 0); analogWrite(_PIN_SPEED_M4, 0); digitalWrite(_PIN_DIR_A_M1, LOW); digitalWrite(_PIN_DIR_B_M1, LOW); digitalWrite(_PIN_DIR_A_M2, LOW); digitalWrite(_PIN_DIR_B_M2, LOW); digitalWrite(_PIN_DIR_A_M3, LOW); digitalWrite(_PIN_DIR_B_M3, LOW); digitalWrite(_PIN_DIR_A_M4, LOW); digitalWrite(_PIN_DIR_B_M4, LOW); }

Questo codice non è ancora stato inserito all’interno del codice di Arduino nel momento della stampa di questo documento, è in fase di testing e abbiamo preferito inserirlo perché è stato fatto del lavoro per realizzarlo. La sua funzione è quella di migliorare la gestione dell’input via Bluetooth per poter realizzare chiamate complesse rispetto a quelle semplici presenti attualmente.

#include <stdio.h>

#include <string.h>

#include <stdlib.h>

#define MAX_CMD_BUFFER 256 #define N_COMANDI 5

// Globale:
char buffer[MAX_CMD_BUFFER];
char * comandi[] = {"ava","sx","ind","dx","standby"};

// stop è il n. di lettere da confrontare
// Restituisce:
// 0 (attesa) fin quando il comando nel buffer (fino alla posizione stop) è parte di un c. conosciuto // 1 (comando riconosciuto)
// -1 (comando inesistente)
int rec(int stop) {
int compar;
for(int i=0; i<N_COMANDI; i++) {
if (strlen(comandi[i])<stop) continue; compar = strncmp(comandi[i],buffer,stop); if (compar==0)
return strlen(comandi[i])==stop; else continue;
}
return -1;
}

void buff_init() {
for (int i=0;i<MAX_CMD_BUFFER; i++) buffer[i]='\0';
}

// Restituisce l'indice del vettore dei comandi a cui si trova il comando attualmente presente nel buffer int get_cmd_number() {
int i;
for(i=0; i<N_COMANDI; i++)
if (strncmp(comandi[i],buffer,strlen(comandi[i]))==0) return i; return -1;
}

int get_param(){
char param_txt[3];
param_txt[0]=getchar();
param_txt[1]=getchar();
param_txt[2]=getchar();
return atoi(param_txt);
}

int main() {
int buffer_pos, cmd_temp;
while (1/*Serial.available() > 0*/){

cmd_temp = -1;
buffer_pos = 0;
buff_init();

do buffer[buffer_pos] = getchar()/*Serial.read()*/;
while (!(cmd_temp=rec(buffer_pos++)) && buffer_pos<MAX_CMD_BUFFER) ;

switch (cmd_temp) {
case 1:
printf("Eseguo: %s\n",comandi[get_cmd_number()]); switch (get_cmd_number()) {
case 0: ; // codice per "ava" printf("parametro: %i",get_param()); break;
case 1: ; // codice per "sx"
break;
// ET CETERA
}; break;
case -1: printf("Comando: %s non riconosciuto\n",buffer); break; default: printf("\n\nFATAL ERROR\n\n");
}
}

return 0;
}

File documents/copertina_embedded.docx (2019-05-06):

Anno accademico 2017/2018

Magni Andrea & Mercanti Davide

Università degli Studi di Milano

Anno accademico 2017/2018

Progetto Sistemi Embedded

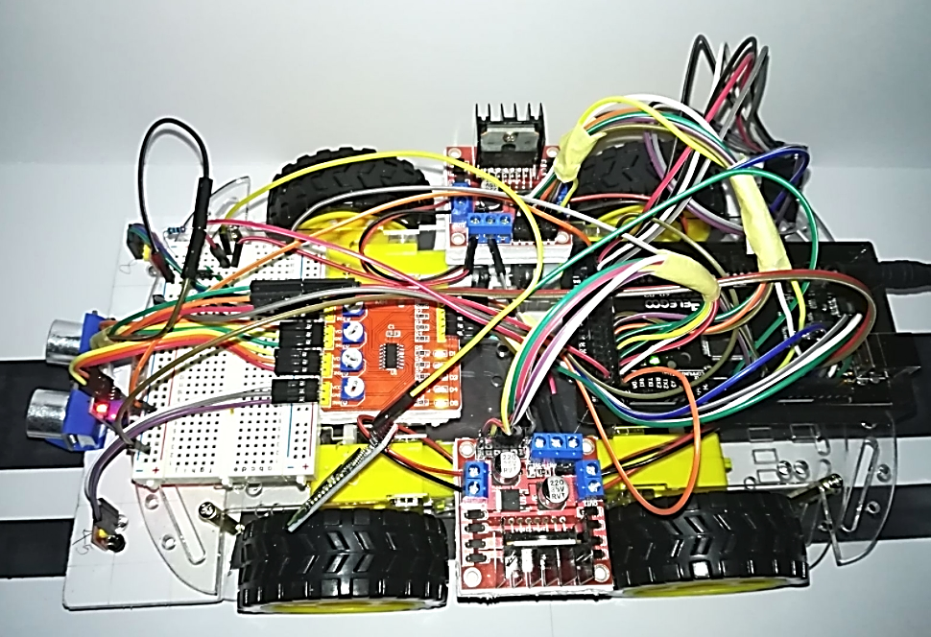
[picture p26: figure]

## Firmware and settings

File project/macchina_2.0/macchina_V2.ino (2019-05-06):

/*
 *  Nome file: macchina_V2.ino
 *
 *  Questo programma permette alla macchina, attraverso diverse funzioni, sensori e moduli di poter valutare
 *  ed interagire con l’esterno. Nello specifico la macchina dovrà riuscire a muoversi all’interno di una strada 
 *  appositamente creata e comunicare attraverso segnali Bluetooth e Radio con altri oggetti.
 *
 *  Informazioni dettagliate sul progetto al seguente link: https://github.com/AndreaMagni/SistemiEmbedded/
 *
 *  Copyright © 2018, Magni Andrea & Mercanti Davide, 14 Marzo 2018
 *
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
 *  You should have received a copy of the GNU General Public License with this program. 
 *  If not, see <http://www.gnu.org/licenses/>.
 */

#include <NewPing.h>
#include "Motor.h"
#include <nRF24L01.h>
#include <printf.h>
#include <RF24.h>
#include <RF24_config.h>

// Ricordare che i sensori ad infrarossi ritornaro - [1] se vedo nero (libero) - [0] se vedo bianco (ostacolo)

#define INFRARED_EXTERNAL_RIGHT 10
#define INFRARED_CENTRAL_RIGHT 11
#define INFRARED_CENTRAL_LEFT 12
#define INFRARED_EXTERNAL_LEFT 13

#define TRIGGER_PIN 7
#define ECHO_PIN 8
#define MAX_DISTANCE 500

#define OBSTACLE_DELAY 5000
#define OBSTACLE_DETECTION_DISTANCE 20 // va considerato il tempo di frenata, prossimo upgrade
#define PING_NUMBER 10 // 20 iterazioni richiedono circa mezzo secondo

NewPing sonar(TRIGGER_PIN, ECHO_PIN, MAX_DISTANCE);
Motor motor(5, 3, 9, 6, 22, 26, 30, 34, 24, 28, 32, 36);
RF24 radio(45, 44);

short obstacle_actual_distance;
bool debug = 0;
bool change_lane = 0;
bool to_right = 0;
bool to_left = 0;
int max_acceptable_loop = 75;
int received_loop;
const byte address[6] = "00001";

void setup () {  
  Serial.begin(9600);
  pinMode(INFRARED_EXTERNAL_RIGHT,INPUT);
  pinMode(INFRARED_CENTRAL_RIGHT,INPUT);
  pinMode(INFRARED_CENTRAL_LEFT,INPUT);
  pinMode(INFRARED_EXTERNAL_LEFT,INPUT);
  radio.begin();
  radio.openReadingPipe(0, address);
  radio.setPALevel(RF24_PA_MIN);
  radio.startListening();    
}

void loop () {
  if (light_status()) {
    if (!change_lane) {
      movement();
      lane_change_process();
    } else lane_reach();
  } else {
    motor.car_stop();
  }
}

//////////////////////////
//                      //
//  Funzioni generiche  //
//                      //
//////////////////////////

bool secure_digital_read(int pin) {
  bool tmp1, tmp2, tmp3;
  tmp1 = digitalRead(pin);
  delay(2);
  tmp2 = digitalRead(pin);
  delay(2);
  tmp3 = digitalRead(pin);
  return ((tmp1 && tmp2) || (tmp2 && tmp3));
}

//////////////////////////////////
//                              //
//  Funzioni gestione semaforo  //
//                              //
//////////////////////////////////

bool light_status() {
  if (radio.available()) {
    unsigned char received_status[7] = "";  
    radio.read(&received_status, sizeof(received_status));
    received_loop = received_status[4];
    if (received_loop >= max_acceptable_loop) {
      if (debug) {Serial.print(" Macchina ferma - Loop "); Serial.println(received_loop);}
      return false;     
    } else return true;
  } 
}

///////////////////////////////////////
//                                   //
//  Funzioni movimento sulla corsia  //
//                                   //
///////////////////////////////////////

bool lane_central_left() {
  if (secure_digital_read(INFRARED_CENTRAL_LEFT)) return true;
  else return false;
}

bool lane_central_right() {
  if (secure_digital_read(INFRARED_CENTRAL_RIGHT)) return true;
  else return false;
}

void movement() {
  if (lane_central_left() && lane_central_right()) motor.car_forward(60);
  else if (!lane_central_left() && lane_central_right()) motor.car_right(85);
  else if (lane_central_left() && !lane_central_right()) motor.car_left(85);
  else motor.car_stop();
}

/////////////////////////////////////
//                                 //
//  Funzioni rilevamento ostacoli  //
//                                 //
/////////////////////////////////////

bool obstacle_presence() {
  unsigned int millisec = sonar.ping_median(PING_NUMBER);
  obstacle_actual_distance = sonar.convert_cm(millisec);
  if (obstacle_actual_distance <= OBSTACLE_DETECTION_DISTANCE) return true;
  else return false;
}

bool obstacle_evaluation() {
  if (obstacle_presence()) {
    motor.car_stop(); 
    delay(OBSTACLE_DELAY);       
    if (obstacle_presence()) return true;
    else return false;
  } else return false;
}

//////////////////////////////
//                          //
//  Funzioni cambio corsia  //
//                          //
//////////////////////////////

void lane_change_to_left() {
  to_left = 1;
  motor.car_backward(65);
  delay(400);
  motor.car_left(140);
  delay(400);
}

void lane_change_to_right() {
  to_right = 1;  
  motor.car_backward(65);
  delay(400);
  motor.car_right(140);
  delay(400);  
}

int lane_detection() {
  if (secure_digital_read(INFRARED_EXTERNAL_LEFT)) return 1;
  else if (secure_digital_read(INFRARED_EXTERNAL_RIGHT)) return 2;
  else return 0; // Upgrade se restituisce zero effettuare manovra
}

void lane_change_process() {
  if (obstacle_evaluation()) {
    change_lane = 1;
    if (lane_detection() == 1) lane_change_to_right();
    else if (lane_detection() == 2) lane_change_to_left();
    else motor.car_stop();
  }
}

void lane_reach() {
  if (to_right) {
    if (secure_digital_read(INFRARED_CENTRAL_LEFT)) {
      to_right = 0;
      motor.car_left(100);
      delay(500);
      motor.car_forward(60);
      delay(1000); 
      change_lane = 0;              
    } else motor.car_forward(60);       
  }
  if (to_left) {
    if (secure_digital_read(INFRARED_CENTRAL_RIGHT)) {
      to_left = 0;      
      motor.car_right(100);
      delay(500); 
      motor.car_forward(60);
      delay(1000); 
      change_lane = 0;           
    } else motor.car_forward(60);           
  } 
}
